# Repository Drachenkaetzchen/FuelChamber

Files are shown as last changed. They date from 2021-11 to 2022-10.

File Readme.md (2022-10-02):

# FuelChamber Toolhead PCB

This is a drop-in remix of [hartk's Afterburner Toolhead PCB](https://github.com/hartk1213/Voron-Hardware/tree/master/Afterburner_Toolhead_PCB) v3.1 with the following changes:

- On-board 12V regulator to allow the operation of 12V fans, selectable for each fan using solder jumpers. Maximum 1A for the 12V rail.
- Pin Compatible with the Afterburner Toolhead PCB
- Decreased height to avoid interference with the Voron 1.8 gantry
- Increased clearance for the mounting screws to avoid damaging the traces

Rev A and Rev B have no support for the BAT85 Diode!

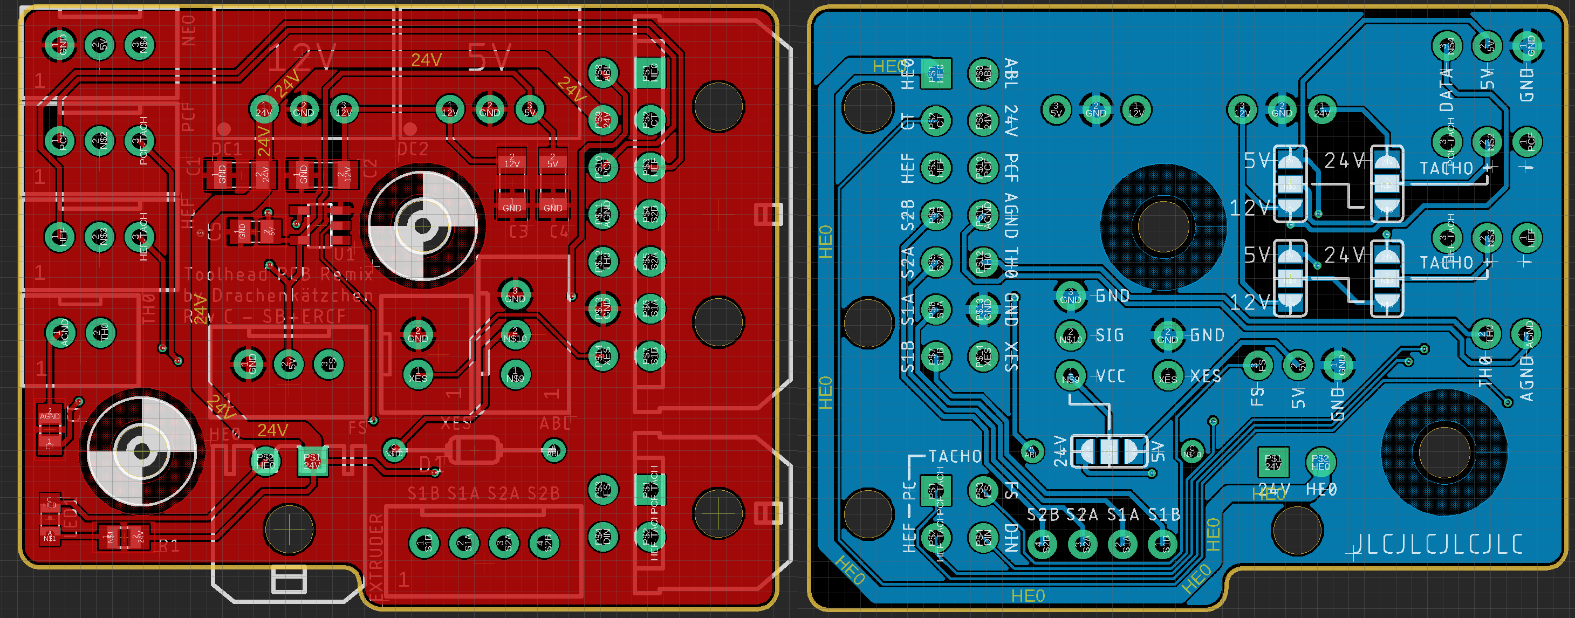
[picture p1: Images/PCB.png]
PCB Renders

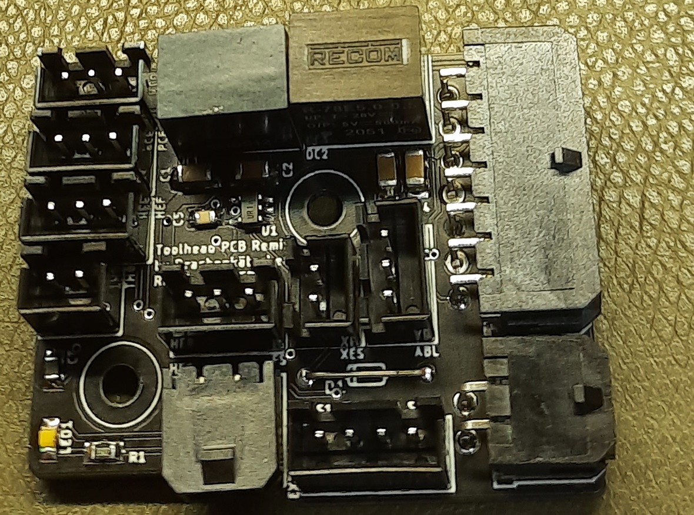
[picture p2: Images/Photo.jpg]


# Usage

This PCB replaces a hartk Afterburner Toolhead PCB. Replace your 24V fans with 12V fans as needed, and use
the solder jumpers to configure the voltage. Simply remove the old PCB and insert this one.

For assembly: Always start with the lowest height components and work your way up.

Note this PCB is `experimental` because it has yet to be determined if the DC/DC converters survive the
constant toolhead movements. Although the VR10S12 did survive for 100 printing hours now, it's unlikely that they fail, but we never know until we try.s

# BOM

## Warning: Outdated!

| Designator | Footprint | Value | Remarks
|---|---|---|---
| C1 | 1206 | 10µF 35V | ceramic caps are okay, too
| CT | 0805 | CMFB103F3950FANT | 10kΩ ±1% 3950K NTC Thermistor
| D1 (for VR10S12 ) | SMB | 22µF 16V | use a 1206 capacitor, 10µF ceramic is often okay, too
| D1 (for R-78C12-1.0) | SMB | 1SMB5928BT3G | as specified by the R-78C12-1.0 datasheet
| DC1 | SIP 3 | VR10S12 | The original design used a Recom R-78C12-1.0, but a XP Power VR10S12 is cheaper
| LED1 | 0805 | LED 0805 | Use any 0805 chip LED, indicates heater activity
| R1 | 0805 | see remarks | Calculate this appropriately for LED1 and 24V!
| HE0, HEF, PCF, XES | JST-XH-02 | 2-pin JST XH |
| ABL | JST-XH-03 | 3-pin JST XH |
| E-STEP | JST-XH-04 | 4-pin JST XH |
| HE0 | MOLEX 436500200 | MOLEX 436500200  |
| - | MOLEX 430451400 | MOLEX 430451400  |		

# Alternative Voltage Regulators

You can use one of these DC/DC voltage regulators if you are having trouble finding the `VR10S12`. Please refer
to the datasheet for any input/output decoupling.

__Please do not use any linear voltage regulators, because these require a heatsink and the acceleration forces will most likely shear off the voltage regulator over time.__

## 1A DC/DC Converters

- Traco Power `TSR 1-24120`
- Recom `R-78C12-1.0`

## 500mA DC/DC Converters

Use these only if you are sure that your fans will not exceed the current capability! The peak current when
the fans are starting up can be higher than specified!

- Aimtec `AMSR-7812-NZ`
- Traco Power `TSR 0.5-24120`
- XP Power `SR05S12`
 
# Design Notes

- The trace widths are calculated to allow operation within a 70°C chamber and a maximum temperature
  rise of 10°C.
- The pin assignments of the 14 pin MicroFit3 connector is unchanged
- The original version used a Recom R-78C12-1.0, but has been changed to a VR10S12 which lowers the cost significantly
- I've been using the Rev.A with a VR10S12 for about 100 hours of printing in conjunction with a single 12V fan, no issues observed so far

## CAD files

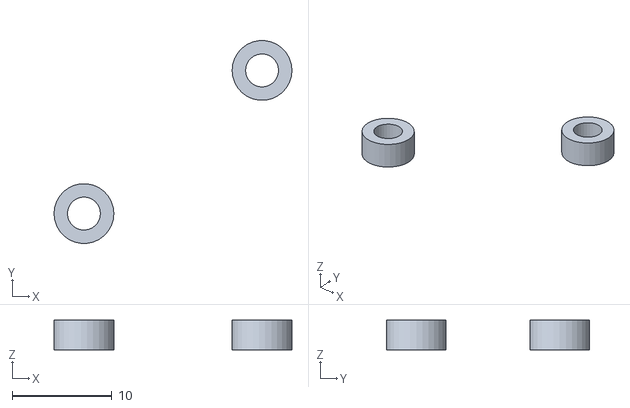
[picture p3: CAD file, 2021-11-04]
STL/spacers.stl
23.8 x 20.3 x 3.00

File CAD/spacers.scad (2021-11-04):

$fn = 30;

// 1 for the original hartk PCB to avoid the screws scratching up traces
// 3 as spacer between the PCB and the extruder

height=3;

holePos1_x = 64.89;
holePos1_y = 58.92;

holePos2_x = 82.73;
holePos2_y = 73.26;

holeDiam = 3.3;
outerHoleDiam = 6;




difference () {
mkholes(outerHoleDiam);
mkholes(holeDiam);
}

module mkholes (diam) {
translate([holePos1_x, holePos1_y]) { 
cylinder(d=diam,h=height);
}

translate([holePos2_x, holePos2_y]) { 
cylinder(d=diam,h=height);
}
}

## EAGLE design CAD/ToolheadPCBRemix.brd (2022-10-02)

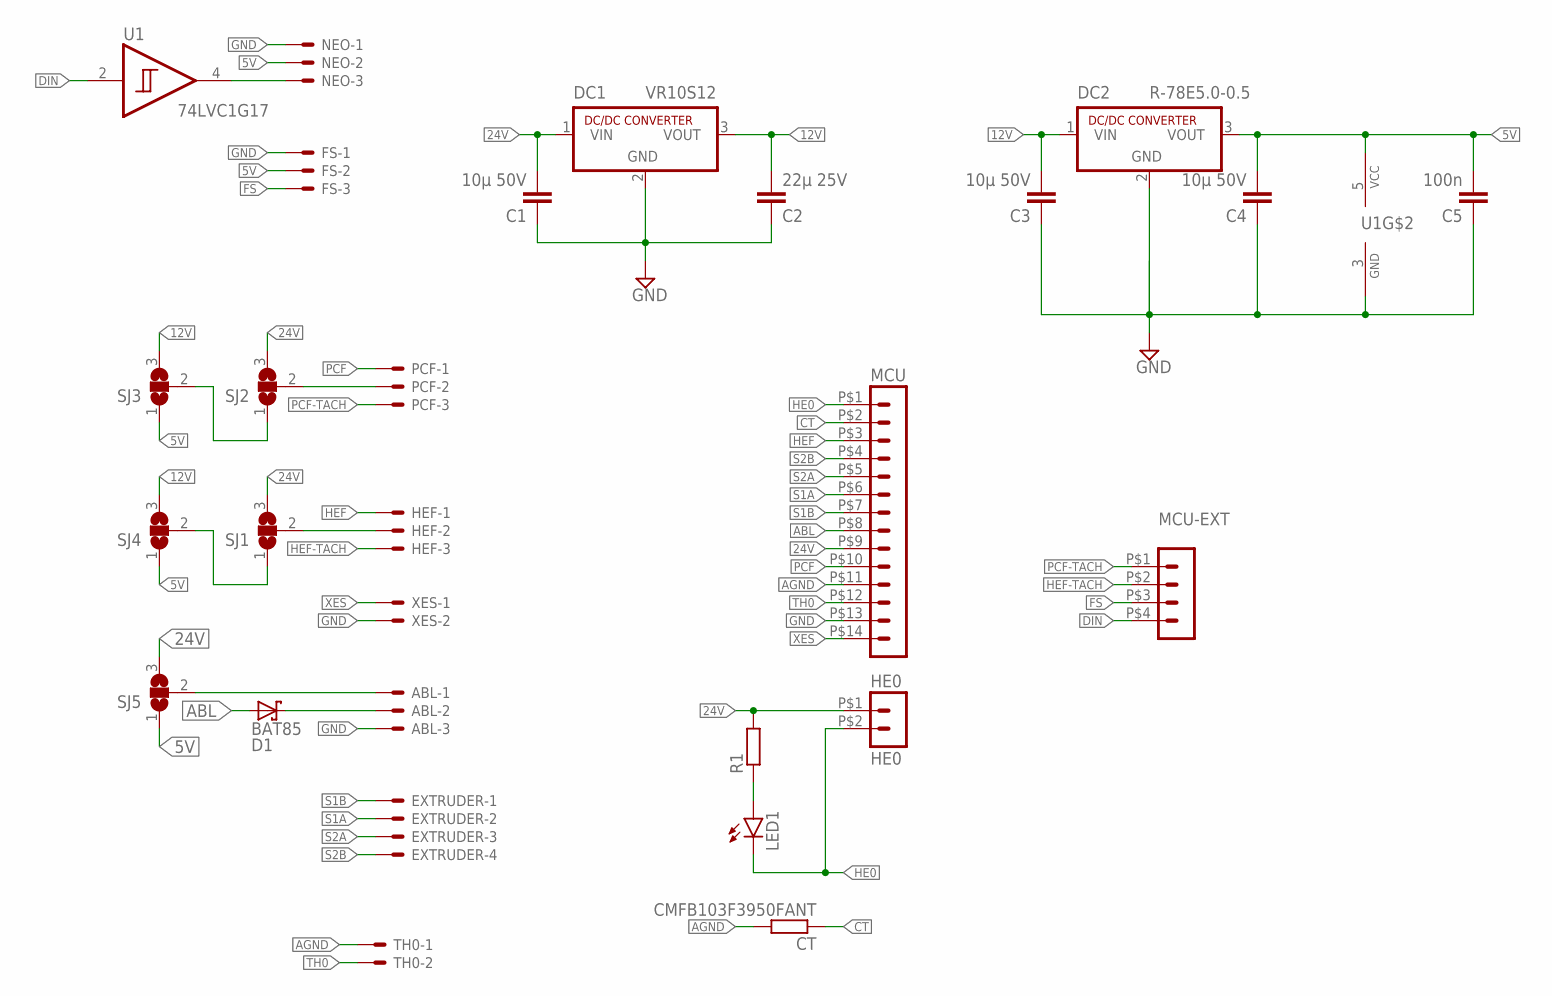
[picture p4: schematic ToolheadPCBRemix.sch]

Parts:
ABL: JST-XH-03-PIN-ROUND-PAD; JST-XH-03-PACKAGE-ROUND-PAD
C1, C3, C4: 10µ 50V; C1206
C2: 22µ 25V; C1206
C5: 100n; C0805
CT: CMFB103F3950FANT; R0805
D1: BAT85; SOD68
DC1: VR10S12; SIP3
DC2: R-78E5.0-0.5; SIP3
EXTRUDER: JST-XH-04-PIN-ROUND-PAD; JST-XH-04-PACKAGE-ROUND-PAD
FS: JST-XH-03-PIN-ROUND-PAD; JST-XH-03-PACKAGE-ROUND-PAD
HE0: HE0; 43650-0200
HEF: JST-XH-03-PIN-ROUND-PAD; JST-XH-03-PACKAGE-ROUND-PAD
LED1: LEDCHIPLED_0805; CHIPLED_0805
MCU: HEADER_POS14_43045-1400; 43045-1400
MCU-EXT: HEADER_POS4_43045-0401; 43045-0400
NEO: JST-XH-03-PIN-ROUND-PAD; JST-XH-03-PACKAGE-ROUND-PAD
PCF: JST-XH-03-PIN-ROUND-PAD; JST-XH-03-PACKAGE-ROUND-PAD
R1: R-EU_R0805; R0805
SJ1, SJ2, SJ3, SJ4, SJ5: SJ2W; SJ_2
TH0: JST-XH-02-PIN-ROUND-PAD; JST-XH-02-PACKAGE-ROUND-PAD
U1: 74LVC1G17; SOT23-5
XES: JST-XH-02-PIN-ROUND-PAD; JST-XH-02-PACKAGE-ROUND-PAD

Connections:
5V: C4.2, C5.2, DC2.3 (VOUT), FS.2, NEO.2, SJ3.1, SJ4.1, SJ5.1, U1.5 (VCC)
12V: C2.2, C3.2, DC1.3 (VOUT), DC2.1 (VIN), SJ3.3, SJ4.3
24V: C1.2, DC1.1 (VIN), HE0.P$1 (1), MCU.P$9 (9), R1.2, SJ1.3, SJ2.3, SJ5.3
ABL: D1.A, MCU.P$8 (8)
AGND: CT.2, MCU.P$11 (11), TH0.1
CT: CT.1, MCU.P$2 (2)
DIN: MCU-EXT.P$4 (4), U1.2 (A)
FS: FS.3, MCU-EXT.P$3 (3)
GND: ABL.3, C1.1, C2.1, C3.1, C4.1, C5.1, DC1.2 (GND), DC2.2 (GND), FS.1, MCU.P$13 (13), NEO.1, U1.3 (GND), XES.2
HE0: HE0.P$2 (2), LED1.C, MCU.P$1 (1)
HEF: HEF.1, MCU.P$3 (3)
HEF-TACH: HEF.3, MCU-EXT.P$2 (2)
unnamed: LED1.A, R1.1
unnamed: PCF.2, SJ2.2
unnamed: HEF.2, SJ1.2
unnamed: NEO.3, U1.4 (Y)
unnamed: SJ2.1, SJ3.2
unnamed: SJ1.1, SJ4.2
unnamed: ABL.1, SJ5.2
unnamed: ABL.2, D1.C (K)
PCF: MCU.P$10 (10), PCF.1
PCF-TACH: MCU-EXT.P$1 (1), PCF.3
S1A: EXTRUDER.2, MCU.P$6 (6)
S1B: EXTRUDER.1, MCU.P$7 (7)
S2A: EXTRUDER.3, MCU.P$5 (5)
S2B: EXTRUDER.4, MCU.P$4 (4)
TH0: MCU.P$12 (12), TH0.2
XES: MCU.P$14 (14), XES.1

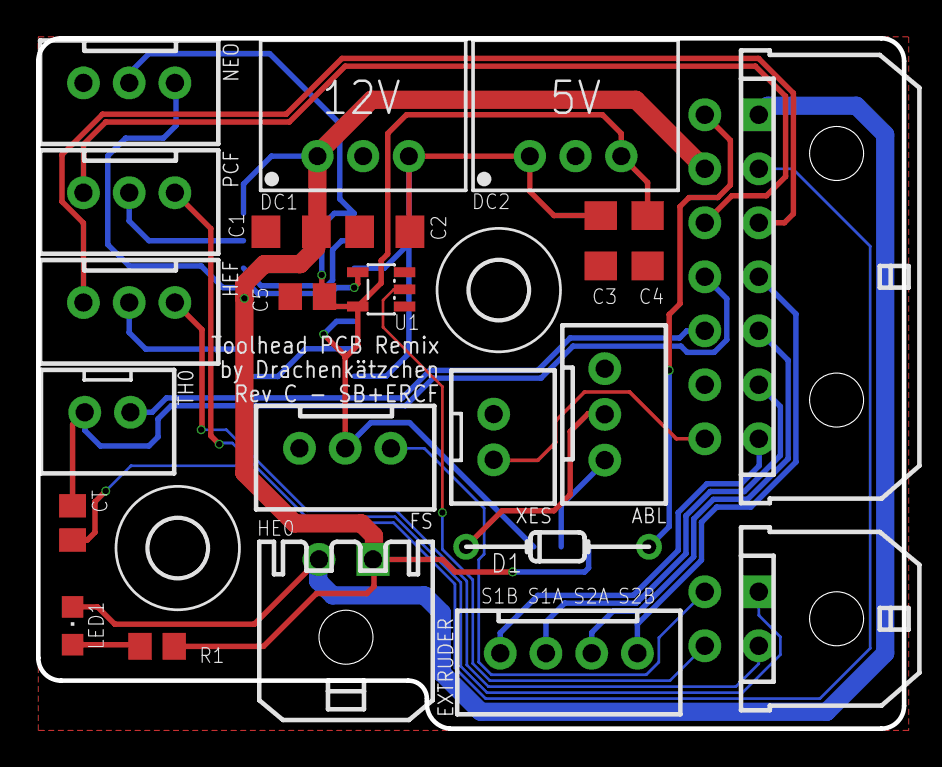
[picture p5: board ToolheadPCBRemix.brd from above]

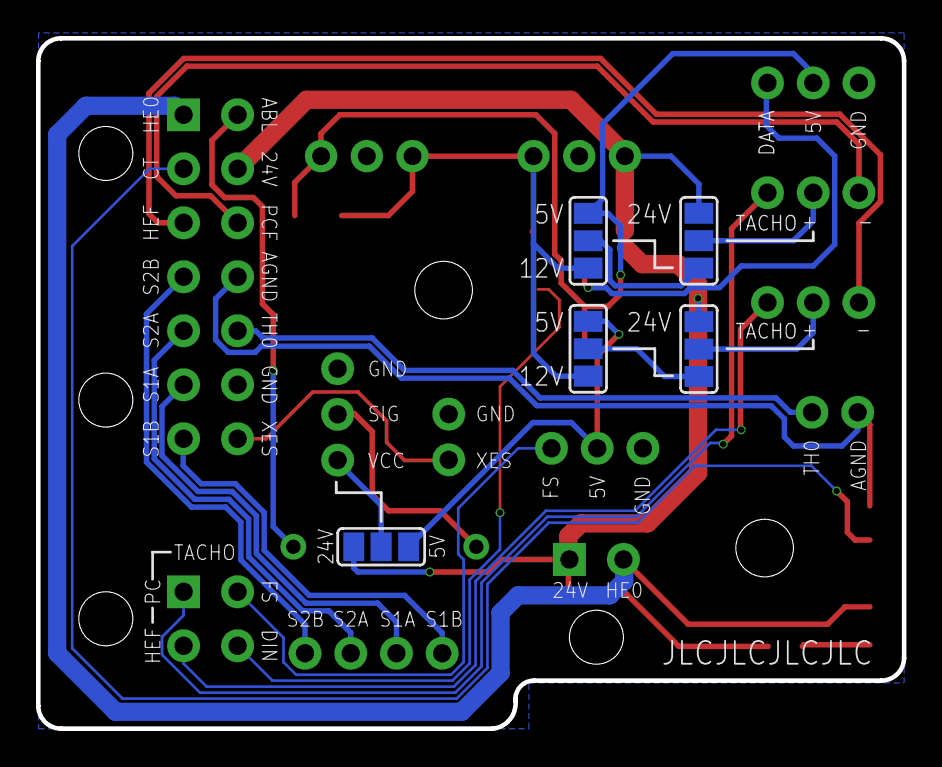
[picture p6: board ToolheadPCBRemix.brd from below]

Board: 2 copper layers, 48.1 x 38.4 mm, 30 parts (5 on the bottom side), 28 nets.

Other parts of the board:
E$1, E$2: 3,2

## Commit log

2022-10-02 Update to dual vregs (12V/5V)
    [ToolheadPCBRemix.brd, ToolheadPCBRemix.sch]
2022-10-02 Fixed PCB imge path
